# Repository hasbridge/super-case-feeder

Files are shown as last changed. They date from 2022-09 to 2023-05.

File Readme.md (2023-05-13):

## Super Case Feeder

This case feeder is designed for the Hornady Lock-n-Load AP progressive reloading press. It works with virtually any caliber that will fit down Lee case feeder tubes, from 380 ACP to 30-06. 

Demo of press in action: https://www.youtube.com/watch?v=Jn4G6Q33BeE

Case Feeder Assembly

## Features
- Can handle any case length between 17mm and 63mm in length, and between 7 and 13.5mm in diameter
- Case dropper with hinged doors to quickly change calibers, no need for different caliber inserts
- Collator with 6 tubes holds over 100 cases of 9mm or 45 ACP
- Lower slider is quickly removable for hand-feeding cases, and can be stored on the back of the case feeder assembly

## Bill of Materials

Most parts can be sourced from a local hardware store, and can all be easily sourced online. The ball detent is optional, and a 3d printable plastic detent STL file is included which can be used in it's place if desired.

- M4x25mm Screw (8)
- M4x15mm Screw (1)
- M4 Lock Nut (1)
- M3x50 Screw (2)
- 1/4-20 x 6" Bolt (1)
- 1/4-20 Nut (1)
- 1/4-20 x 3/4" Bolt (2)
- 1/4" Fender Washer (2)
- 624 Bearing (1)
- Hillman #6 Spring (1) (https://www.farmandfleet.com/products/512679-hillman-6-spring.html)
- Hillman #9 Spring (1) (https://www.farmandfleet.com/products/512680-hillman-9-spring.html)
- 6mm ball detent assembly (optional) (https://www.amazon.com/dp/B07CCN8WWJ)
- Lee Case Feeder 7 Tube Set (1) (https://www.amazon.com/dp/B000N8JWEO)

## Recommended Print Settings
- PETG is recommended, but PLA should work as well
- ~0.24 Layer height, with ~40%+ infill for strength
- STL files are all rotated for correct printing orientation
- Supports are not needed except for a small amount on the lower slider nose

## Files To Print
All files needed to print the standard configuration are in the **Base STL Files** folder. This includes everything needed to complete the case feeder. For custom configurations such as using with a motorized case collator, files are available in the **Mods** folder.

## Assembly

See the wiki page for assembly instructions at https://github.com/hasbridge/super-case-feeder/wiki/Assembly-Instructions

## License

You are free to print and modify the files for personal, non-commercial use. Selling copies or printed parts is not authorized without explicit permission from the original author.

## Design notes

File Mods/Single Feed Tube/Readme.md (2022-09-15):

## Single Feed Tube Mod

This mod will allow you to use a motorized case collator such as the BF556. The 2 files replace the standard 6-tube collator and tube assembly with a single Lee case feeder tube. This tube can be cut to length and connected to any motorized collator.



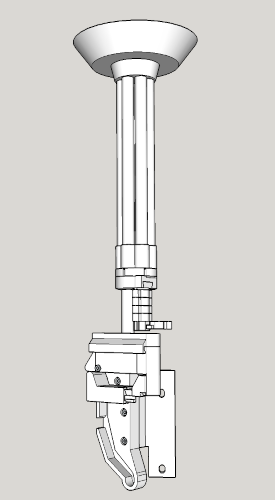
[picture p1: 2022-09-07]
Universal Case Feeder.png

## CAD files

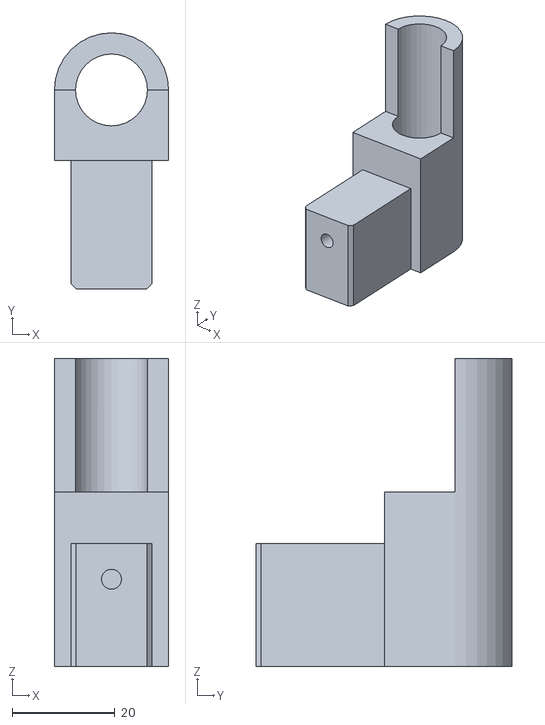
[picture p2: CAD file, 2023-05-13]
Base STL Files/Upper Body Insert.stl
22.3 x 49.9 x 60.0

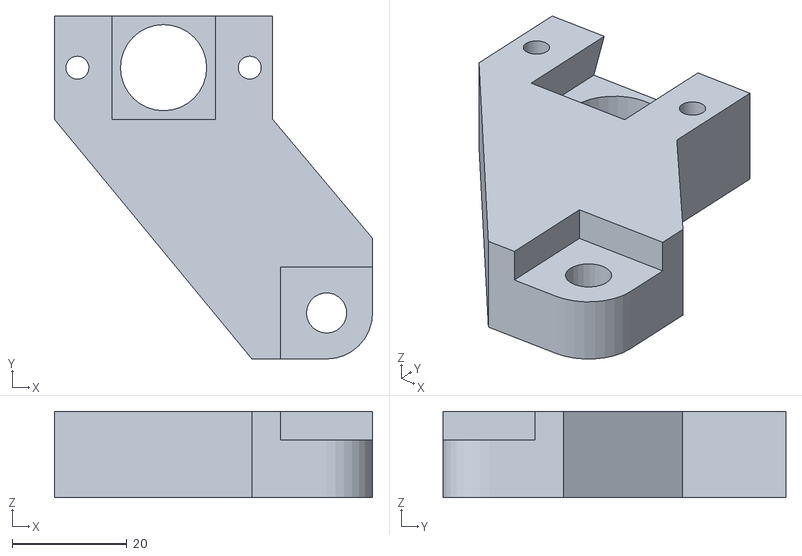
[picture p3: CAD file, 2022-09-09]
Mods/Single Feed Tube/Single Tube Stand Base.stl
55.4 x 59.7 x 15.0

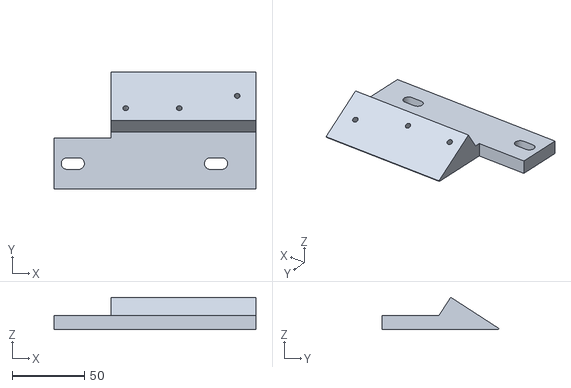
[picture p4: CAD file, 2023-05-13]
Base STL Files/Mounting Bracket.stl
139.5 x 81.0 x 22.4

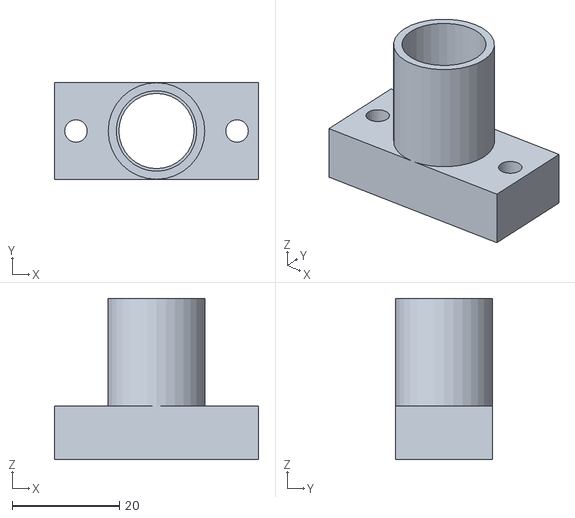
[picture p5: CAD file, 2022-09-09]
Mods/Single Feed Tube/Single Tube Stand Lee Tube Adapter.stl
38.0 x 18.0 x 30.0

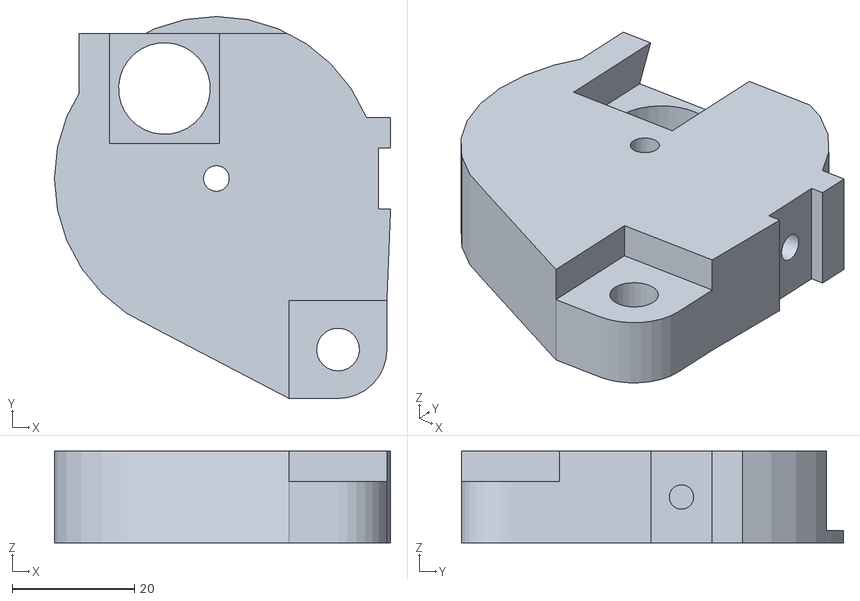
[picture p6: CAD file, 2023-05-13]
Base STL Files/Tube Stand Base.stl
55.0 x 62.5 x 15.0

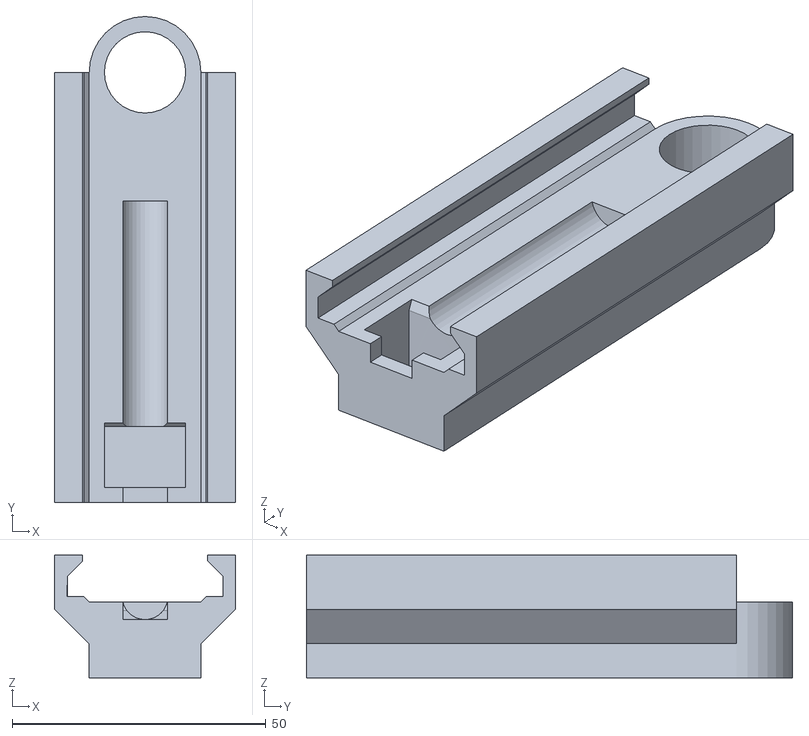
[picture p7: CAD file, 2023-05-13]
Base STL Files/Upper Slider.stl
35.7 x 95.7 x 24.2

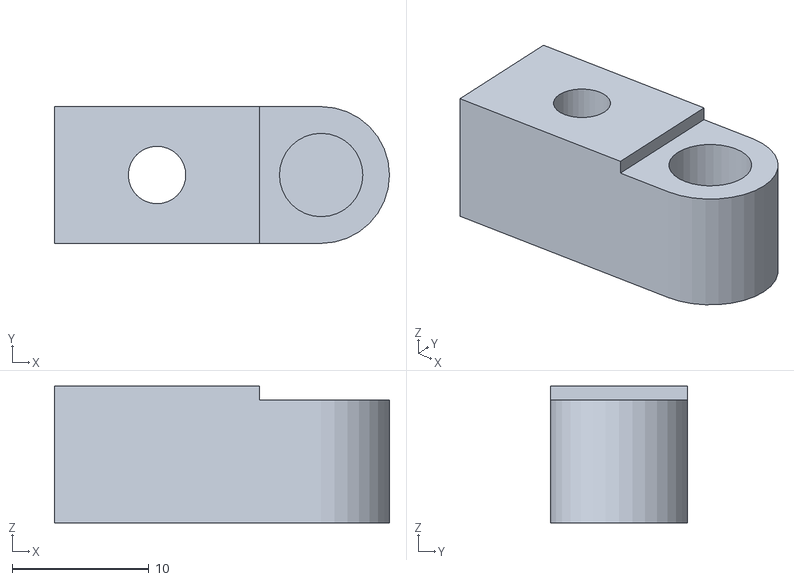
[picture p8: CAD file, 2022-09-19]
Base STL Files/Ball Detent Housing.stl
24.5 x 10.0 x 10.0

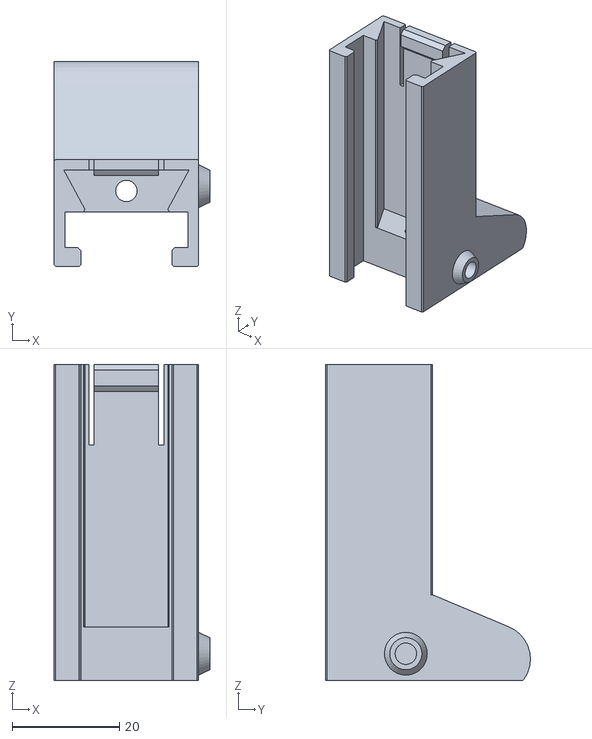
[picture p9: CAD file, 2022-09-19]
Base STL Files/Lower Slider.stl
29.1 x 38.3 x 59.0

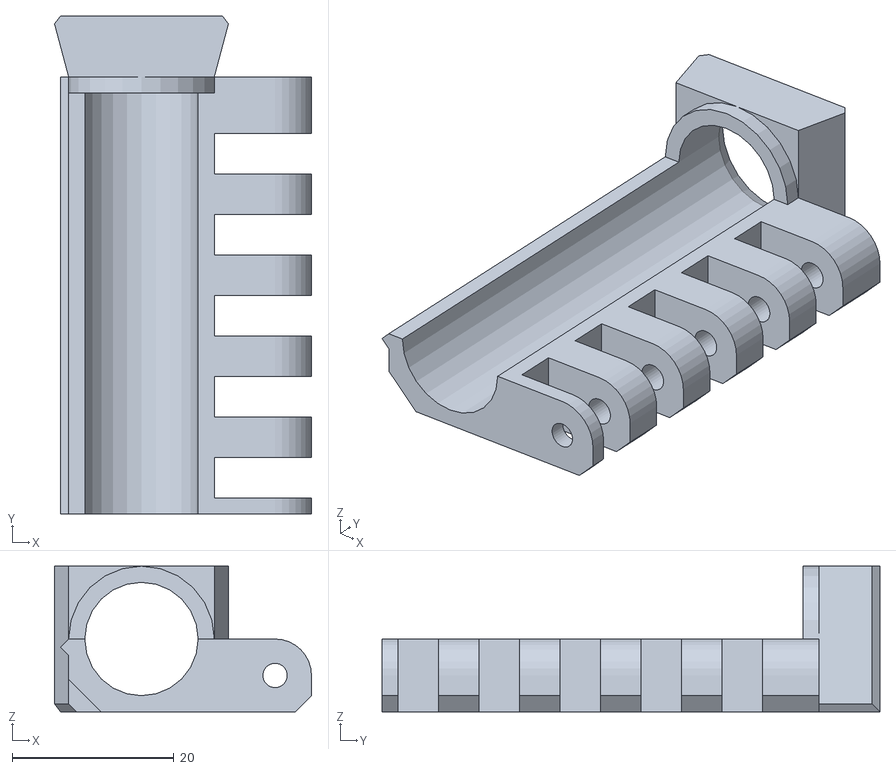
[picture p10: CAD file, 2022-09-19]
Base STL Files/Case Dropper Insert.stl
31.7 x 61.5 x 18.0

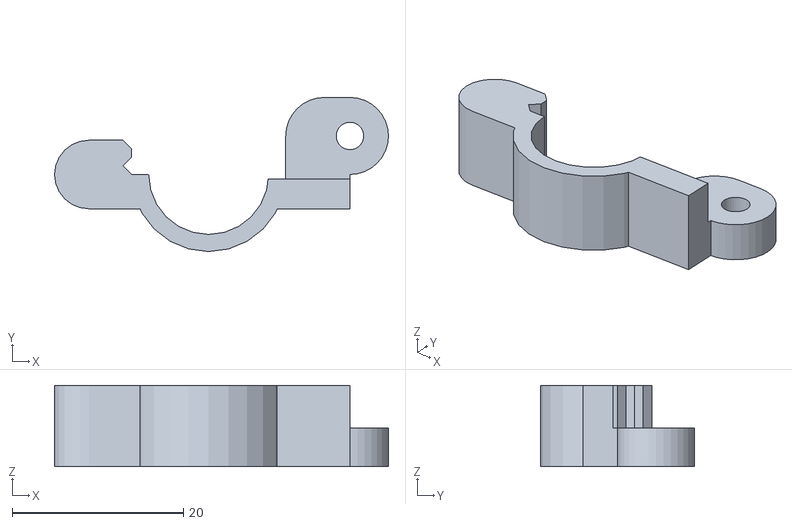
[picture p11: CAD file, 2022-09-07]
Base STL Files/Case Dropper Door.stl
39.0 x 18.0 x 9.50

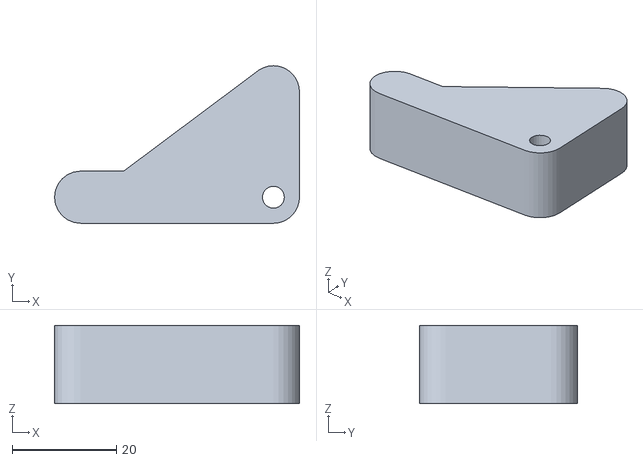
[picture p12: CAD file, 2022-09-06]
Base STL Files/Bellcrank.stl
47.0 x 30.2 x 15.0

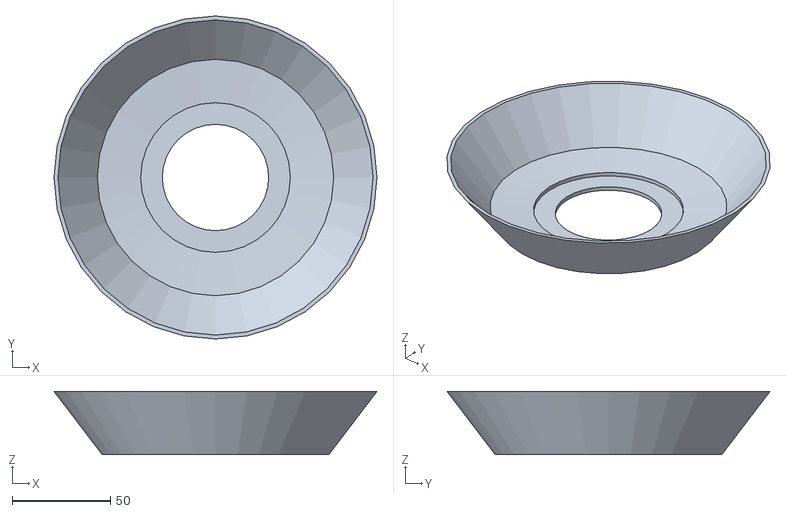
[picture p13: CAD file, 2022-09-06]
Base STL Files/Collator Bowl.stl
164.0 x 164.0 x 32.0

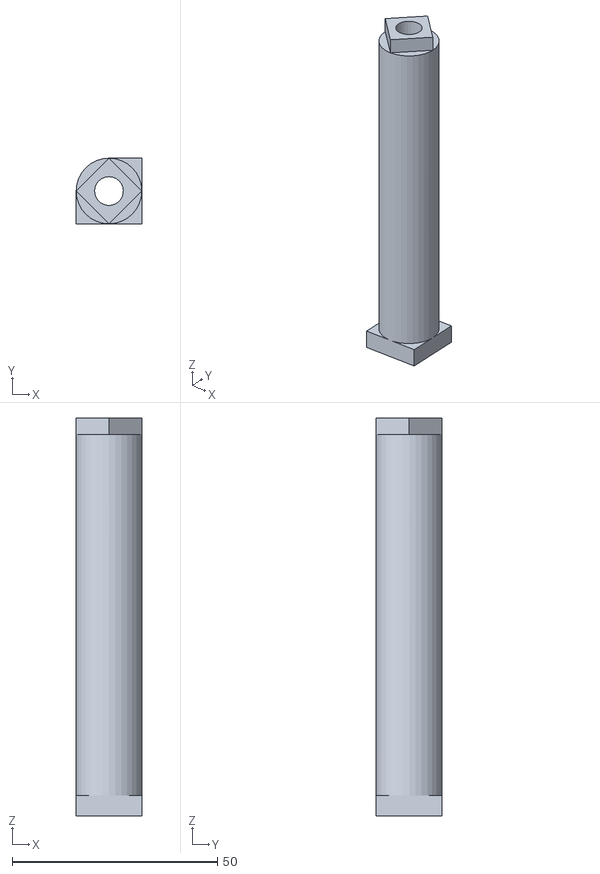
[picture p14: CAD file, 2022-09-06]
Base STL Files/Tube Stand Riser.stl
16.0 x 16.0 x 97.0

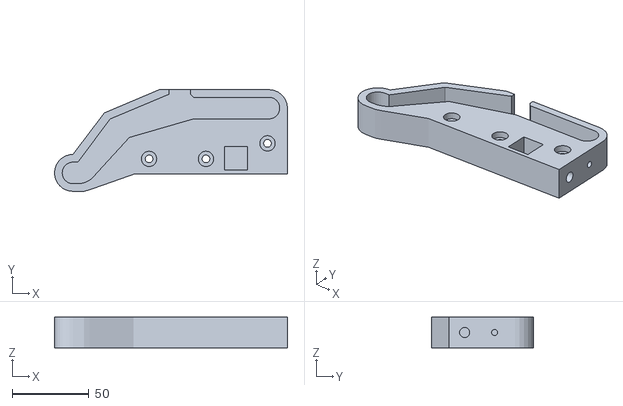
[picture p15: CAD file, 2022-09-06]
Base STL Files/Cam Track.stl
151.5 x 66.1 x 20.0

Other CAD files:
Base STL Files/Collator Base.stl
Base STL Files/Lower Slider Nose.stl
Base STL Files/Tube Selector.stl
Base STL Files/Upper Body.stl
Base STL Files/Collator Insert.stl
Base STL Files/Plastic Detent.stl

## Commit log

2022-09-07 add more clearance for case dropper door hinges
    [Case Dropper Door.stl]
2022-09-07 add clearance for hinge to rotate easier
    [Case Dropper Door.stl]
2022-09-09 adding mod for single-tube stand, and single lee tube adapter
    [Single Tube Stand Base.stl, Single Tube Stand Lee Tube Adapter.stl]
2022-09-15 organize files better, add readme for mod
    [Ball Detent Housing.stl, Bellcrank.stl, Cam Track.stl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]
2022-09-15 update readme, rename collator insert
    [Collator Insert.stl]
2022-09-19 rotate lower slider for correct print orientation, adjust insert screw hole size, enlarge ball detent hole size, reinforce detent mounting support
    [Ball Detent Housing.stl, Case Dropper Insert.stl, Lower Slider.stl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]
2023-05-13 Lengthen slotted mounting holes by 5mm to allow for variance in mounting hole locations.
    [Mounting Bracket.stl, Tube Stand Base.stl, Upper Body Insert.stl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]
